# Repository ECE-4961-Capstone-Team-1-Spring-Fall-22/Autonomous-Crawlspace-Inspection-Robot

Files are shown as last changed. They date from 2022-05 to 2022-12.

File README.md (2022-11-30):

# Autonomous-Crawlspace-Inspection-Robot
This GitHub contains all relevant files used during development. For a comprehensive guide to the repository set up see the bottom of the document.
## Executive Summary
Crawl spaces grant convenient access to the plumbing, duct work, and electrical wiring of a house, but they often present unique dangers to maintenance professionals and residents alike. Exposure to harsh breathing conditions, hanging obstacles, uncomfortable working positions, and even animals can cause non-ideal conditions. This capstone project will focus on the design and assembly of a robot prototype that can perform these inspections autonomously. The end product will be an autonomous, mobile robot that can be left unattended in a crawlspace by an inspector. It will navigate through the space, create a map and model of the space, compile an image of the entire crawlspace ceiling, and collect sensor data. This sensor data will include humidity, temperature, and wood moisture content.

## Current Robot Capabilities
The first iteration of the project focused on setting up the hardware systems. Sensors, microcontrollers, motors, and power circuits were designed and implemented as part of a larger multi-group project. The following details the current capabilities of the robot.

* Low-level autonomy which allows the robot to navigate through an enclosed area
* Creating a map of the area using the SLAM algorithm
* Take pictures throughout an area and stitch simple areas into a singular, larger image
* Collect humidity, temperature, and moisture content data and overlay information on images
* Supply power for consistent operation across all components
* Robot movement through serial commands and return encoder data to the main microcontroller
* Manual control through text-based commands while also streaming live video to the operator

For more detail on current designs, see files in sub-system directories

## Salient Outcomes
Although this project includes lofty long-term goals, many exceptional systems were able to be incorporated in the first iteration of the project.
* The mapping was found to be accurate to 93% or more in each test that was run. While this is useful information for an inspector to have, it will also provide an invaluable framework for future updates to the autonomy
* Power was successfully applied to all parts of the system with no over-currents or under-voltages experienced by the system. All back EMF from the motors was successfully filtered out as well.
* Environmental sensing was found to be exceptionally accurate. Temperature and Humidity were both found to be 96% accurate or greater while moisture content was successfully measured to within 2.5% moisture.

## Pictures and Videos
The final system demo in the crawlspace can be found [here](https://www.youtube.com/watch?v=mYopD1X_bd8&t=9s)

A picture of the final system can also be found below 

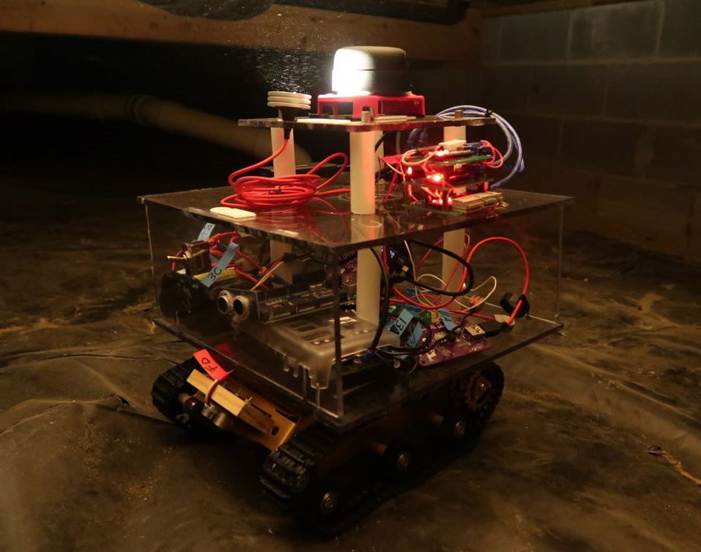
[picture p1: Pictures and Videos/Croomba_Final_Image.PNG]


## Who Are We? Mr. Jesse Robert's ECE 4961 Capstone Team 1

* James (Jim) Camp - Senior Electrical Engineering Major, Mechatronics Concentration - Environmental Sensor Subsystem Developer - Delegator 
* John-Caleb (JC) Williams - Senior Electrical Engineering Major, Electromagnetics Concentration - Navigation Subsystem Developer - Treasurer
* John Harris - Senior Electrical Engineering Major, Controls Concentration - Power Subsystem Developer - Secretary
* Joseph Thomas - Senior Electrical Engineering Major, Power Concentration - Movement Subsystem Developer - Social 

* Mr. Jesse Roberts - Professor and Faculty Advisor

* Project Stakeholders - This project was developed for anyone who needs to inspect their crawlspace. This includes homeowners, building inspectors, and renovators. The system is also a great solution for anyone experiencing issues with mold or unsafe crawlspace conditions.

# Repo Guide
This repository contains the entirety of the Autonomous Crawlspace Inspection Robot’s REV1 design files. The folder breakdown is as follows
* Design Files – Contains files that represent the final design state of the project. This is made up of an overall system schematic and the bill of materials (BOM).
* Documentation – Contains all written submissions created throughout both semesters of the course. Also included are the presentations used at the end of the project.
* Environmental Sensing – This subsystem is responsible for the data collection which occurs throughout the crawlspace. Additionally, image stitching is also included within this folder.
* Movement – This subsystem is responsible for controlling the physical motion and positioning of the robot. 
* Navigation – This system handles the mapping and autonomy. Interfacing with the Raspberry Pi, LIDAR, distance sensors, and remote access are also included in this subsystem.
* Pictures and Videos – A repository for all the pictures and videos taken throughout the experimentation and testing.
* Power - This subsystem is responsible for providing continuous power to all the components. Circuit protection and power filtering are also integrated into this subsystem.

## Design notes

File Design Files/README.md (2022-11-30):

# Design Files
This folder contains the system-wide designs as shown in a schematic diagram. It also includes the bill of materials (BOM).

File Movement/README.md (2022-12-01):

# Mechanical Movement System
The mechanical movement subsystem is essential for the operation 
of the Autonomous Crawlspace Inpsection Robot. The main purpose
of this system is to provide the robot with the ability to move.

# Specs, Design, and Analysis: 
This system has been designed to:

Communicate with the Navigation System where it receives directional instructions and sends back an instantaneous speed

Fit within the 16 inch height constraint and house all the hardware

Allow for variations in motor speed by using pulse width modulation

Move the robot forwards and backwards, and turn left and right

# Descriptions
An Arduino Mega is the microcontroller for this system. It communicates with the Navigation system, sends signals to the motor drivers, and measures the speed.

The design for the robot's chassis started with a robotics kit purchased from amazon, but it was customized and turned into the towered, modular design that is present today.

The Motor Drivers for the robot are the Cytron MD20A, which is an H-Bridge that can control the polarity of power applied to the motor as well as the average voltage through PWM.

The driving DC gearmotors are from pololu. They come equipped with quadrature hall effect motor encoders that can be used to measure the speed and direction of the robot.

This README file constitutes a summary, for detailed design information and analysis of each component see signoff files in this repository. A seperate README exists for the software in the relevant sub-directory.

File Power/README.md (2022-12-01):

# Autonomous-Crawlspace-Inspection-Robot
This branch documents the design process for the power subsytem. 

# Specs, Design, and Analysis: 
This system had the following requirements
* Provide +5V power to the logic electronics and microcontrollers
* Provide +12V power to the motor and mechanical system
* Prevent surges from creating system-wide failures
* Filter inconsistencies from the battery supply voltage and provide steady DC voltage to the components

The design of the system involved custom buck converters which allowed the use of both +12V and +5V power.
Fuses were used to ensure that power surges from one component would not negatively impact the other subsystems.
Terminal blocks were also used for their secure connections and ability to disconnect if changes were made. 

Analysis for the system can be found in the experimental data file.

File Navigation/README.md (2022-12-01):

# Navigation Subsystem 

## Specs, Design, and Analysis: 

This system is designed to use LiDAR and Ultrasonic distance sensors to navigate the inspection robot throughout a model crawl space while creating a detailed map of the surrounding environment. Additionally, the Navigation Subsystem handles USB communication with Arduino Mega/Nanos included in the Movement and Environmental Sensing Subsystems. The Navigation Subsystem MCU, sensors, wireless access point, and imaging hardware were chosen as hardware components capable of processing graphical heavy processing loads, complex distance measurements, and long-range communication protocols.  

The main MCU was required to run Ubuntu 20.04, the Robot Operating System (ROS), and visually heavy programs such as RVIZ and Gazebo. The 4 GB Raspberry Pi 4B was chosen for the Navigation Subsystem, as the CPU speed and RAM size were thought to be plenty for any computational needs. 

The distance sensors were needed to supply Python and ROS with exact and meaningful distance measurements that could be used to effectively guide the inspection robot throughout the crawl space. Moving at roughly 1 foot per second, the distance sensors were only required to supply 2 samples/second (via the Nyquist Theorem). The 360 Degree Slamtec RPLiDAR was chosen due to its high sampling frequency (KHz range), modularity, and readily available python based packages. The SeeedStudio Grove Ultrasonic Sensor was chosen due to the sensor output voltage of 3.3 Volts (maximum RPI GPIO Pin Voltage) and the included noise-filter for distance measurements.  

The wireless access point was needed to supply either a 2.4 or 5 GHZ wireless network, per FCC communication regulations. Additionally, the wireless access point (WAP) needed to supply a minimum communication range of at least 70 feet and a transmission speed of at least 100 mbps. The TP-Link N300 was chosen due to its maximum wireless transmission speed of 300 mpbs and its size, modularity, and power requirements (5 Volt 1 Amp).  

The camera was needed to provide detailed 720p or 1080p images and live video-feed for manual operation of the inspection robot. Additionally, the camera needed to be equipped with a medium/wide angle lens for capturing a large amount of information in the image of the crawl space ceiling. The camera also needed to be lit by a LED light so that the images would have enough illumination for post-processing and analysis. The SVPro 60 Degree HD USB Camera was selected for the imaging hardware due to its capability for high resolution images and fast autofocus. The Voltaic LED USB Emergency Light was chosen as the lighting hardware due to its modularity, size, light intensity, and power requirements (5 Volts 400 milliAmps).  

## Navigation Subsystem Components

Raspberry Pi 4B 4GB (Main MCU) 

Slamtec 360 Degree LiDAR (Distance Sensor) 

SeeedStudio Grove Ultrasonic Sensors (Distance Sensor) 

TP-Link N300 Travel Router (Wireless Access Point) 

SVPro HD USB 1080p Cameras (Ceiling/Wall Visual Capture Device) 

Voltaic USB LED Emergency Light (Camera Illumination) 

## Software, Signoffs, and Subsystem Schematic
The “Software” folder contains the Navigation Python script used to navigate throughout the crawl space, communicate with the Movement Subsystem Arduino, and take images of the crawl space ceiling. Also, this script allows the user to see live video-feed from the wall-oriented HD Camera if manual control is needed.  

The “Signoff” folder contains research, analysis, and validation of the chosen components  adherence to given constraints and specifications of the Navigation Subsystem.  

The “Schematic” folder contains a detailed KiCAD schematic of the Navigation Subsystem.

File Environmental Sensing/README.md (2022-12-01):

# Enviromental Sensing System

## Specs, Design, and Analysis:
This system is designed to collect 3 types of sensor data while also taking pictures of the crawlspace ceiling. The sensor data consists of the following
* Humidity
* Temperature 
* Wood moisture content

The humidity and temperature system consits of prebuilt sensors which interface with Arduino microcontrollers. However, the mositure content probe had to be custom built. It was made by creating a voltage divider that can switch the value of R1 depending on the range needed to measure. These three sensors each used their own microcontroller to maintain modularity.

A board stack was deisgned to allow for simple interfacing between the sensor modules. This works by using 3 PCBs which are sized the same and can be mounted on top of each other using 1 inch tall standoffs. The power connections for each board are passed throughout the staack using header pins with a long tail. This also allows for any new sensors to be snapped on top of the existing sensors and easily added to the system.

The final part of this subsystem is the image collection. Pictures are taken throughout operation and associated to a set of sensor data. The moisture content is displayed on each picture before being stitched together. Temperature and humidity are treated as an array and have the averages and standard deviations calculated. These values are then used to determine if any outliers exist and dispaly the location of these outliers on the images.

This README file constitutes a summary, for detailed design information and analysis of each component see signoff files in this repository.
A seperate README exists for the software in the relevant sub-directory.

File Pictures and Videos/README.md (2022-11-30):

## Pictures
This directory contains the pictures taken throughout the testing and experimentation phases of the project. 
This includes the images used for stitching, maps generated by the lidar, and general pictures showing our progress through the design

## Videos
A link to the OneDrive containing our experimental videos is found [here](https://tennesseetechuniversity-my.sharepoint.com/personal/jtroberts_tntech_edu/_layouts/15/onedrive.aspx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)

The final test run performed in a real crawlspace environment can be found [here](https://www.youtube.com/watch?v=mYopD1X_bd8). 
While this presented some challenges not seen in the model crawlspace, it was a test beyond the scope of our original project proposal. It achieved navigation and mapping results consistent with our expectations. The stops robot makes during the test are to allow for picture taking as well as data collection. This will be essential when the moisture probe arm is added to the system.

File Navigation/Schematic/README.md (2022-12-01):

## Navigation Schematic

Enclosed is the full KiCAD schematic of the navigation subsystem of the Autonomous Crawl Space Inspection Robot.

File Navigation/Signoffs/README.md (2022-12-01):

# Navigation Signoffs

Enclosed are the completed signoffs for the navigation subsystem of the Autonomous Crawl Space Inspection Robot. These signoffs were written to justify the chosen components adherence to constraints and specifications of the navigation subsystem. The chosen components for each signoff are listed below: 

## Main MCU
Raspberry Pi 4B 

## LiDAR
Slamtec 360 Degree A1/A2 RPLiDAR 

## Ultrasonic Sensors
Seeedstudio Grove Ultrasonic Ranger V2 

## Wireless Access Point
TP-LINK N300 Travel Router 

## HD Camera
SVPro 60 Degree HD USB Camera 

## Flashlight
Voltaic LED USB Emergency Light

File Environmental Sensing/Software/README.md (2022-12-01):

# Software Writeup

## What the code does
This file contains 4 programs that make up the environmental sensing system's software.
* The Temp Arduino file handles receiving data from the temperature sensor over I2C and sending that data to the main MCU using serial communication.
* The Humidity Arduino file handles receiving data from the temperature sensor over a single digital wire and sending that data to the main MCU using serial communication.
* The MC Arduino file handles the moisture content measurement. This code flips through 5 digital outputs to control the values of R1 in the voltage divider circuit. It takes resistance measurements at each point and averages the acceptable measurements before converting from Ohms to %MC.
* The Stitching python file handles the image stitching. The files are automatically sorted into an array and have their MC values overlaid on the image. The images are then stitched together by manually choosing which pictures were taken consecutively.
- This code also handles reading the temperature and humidity values from a text file, averaging the values, and displaying any values which are outside the acceptable range of 2 standard deviations.

## Dependencies
* Adafruit DHT Library (Arduino Internal)- Used to pull data from the humidity sensor over a single-wire data line. 
* Adafruit MCP9808 Library (Arduino Internal) - Used to pull data from the temperature sensor over I2C protocol. 
* https://github.com/KEDIARAHUL135/PanoramaStitchingP2 - Provided basic algorithm for stitching 2 images together and pulling images into an array.

# Code Instructions
For all Arduino codes, the instructions are the same.
1. Build a circuit using Arduino Nano based on the schematic found [here](https://github.com/ECE-4961-Capstone-Team-1-Spring-Fall-22/Autonomous-Crawlspace-Inspection-Robot/blob/main/Environmental%20Sensing/Environmental%20Sensing%20Schemat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)
2. Pull the Arduino file and place it in a folder with the same name as the code.
3. Download all relevant libraries by going into the "Sketch" menu, choosing "Include Library" and then importing the correct library from Arduinos internal system.
4. Set up the serial port by going into the "Tools" menus and choosing the correct device.
5. Upload code to the board.

The image stitching code instructions are as follows
1. Ensure that OpenCV and python are both downloaded and can successfully compile.
2. Places pictures in the folder called "TestPics" and ensure the folder is in the same directory as the program.
3. Ensure pictures are numbered 0 to max in order of taking.
4. Ensure the stitching lines in the code are set to match the pictures which you want to be stitched.
5. Run code, results will be shown in the plot initially but will be saved upon closing the plot.
* NOTE1: There are additional algorithms commented out that can be seen in this code. Each one was found the work for some cases and not for others.
* NOTE2: While this algorithm works for a straight view of an object, it was found in the late stages of development that perspective changes will cause issues. This is the topic of much research at the moment and further algorithm development will be necessary.

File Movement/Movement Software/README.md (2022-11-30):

# Mechanical Movement Software ReadMe
## What the Software Does
This Arduino Program accepts a serial input that is used to change the direction of the drive motors. 
This program uses Interrupts to measure the frequency of the Motor Encoder Signals.
Those Motor Encoder Signals are then converted to RPMs and Output to Serial.

## Dependencies
This program calls upon no additional libraries or other files.
Some form of serial input to the program is required for motor direction change.

## How to Install
This Program can be Uploaded to an Arduino Mega by using the Arduino IDE.
First, connect a USB cable between your computer and the Arduino Mega.
Second, in the IDE, under Tools, ensure that the board is set to "Arduino Mega or Mega 2560" the processor is the ATmega2560.
Third, ensure that the correct COM port has been selected.
Finally, in the IDE, click upload

## How to Run
The Program will immediately start outputting the speed, and it can be seen in the serial monitor.
The speed will consistently be 0 unless the interrupts are pinging.

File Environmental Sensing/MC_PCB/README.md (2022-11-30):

## Moisture Content Probe Module PCB
Enclosed are the Kicad files for the moisture content sensor PCB. This board is designed to be apart of and sensor board stack which uses the standoff parts found in the BOM. 
Terminal blocks are included to allow connection to the external circuit parts such as the motor driver and probe. Connections for these parts are found in the schematic pdf.

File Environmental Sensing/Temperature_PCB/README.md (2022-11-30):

## Temperature Module PCB
Enclosed are the Kicad files for the temperature sensor PCB. This board is designed to be apart of and sensor board stack which uses the standoff parts found in the BOM.

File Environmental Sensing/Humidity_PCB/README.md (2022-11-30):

## Humidity Module PCB
Enclosed are the Kicad files for the humidity sensor PCB. This board is designed to be apart of and sensor board stack which uses the standoff parts found in the BOM.

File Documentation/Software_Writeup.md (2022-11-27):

# Software Writeup
More detailed software descriptions can be found in the individual subsystem folders. Below is a high-level breakdown of the various software that is integrated into the system

## Navigation
* Autonomy
- Simple autonomy allows the robot to bounce around a space wihtout getting stuck
- Manual control is available through the command terminal in case of failure
* Mapping
- Robot Operating System (ROS) was used along with the SLAM algorithm to create a map
- This map can be visualized in RViz 
* Imaging
- The robot takes images of the ceiling at set intervals as it naviagtes
- These images are stitched together to create a wholistic view of the ceiling
- Live video is also streamed to a remote desktop in case of autonomy failure

## Enviromental Sensing
* Three programs were written for this system, one for each sensor
* The humidity and temperature programs required very simple code
- Programs recieved data from their respective sensors
- Data was sent to the main microcontroller through serial communication
* The moisture content probe took a resistance measurement
- This was done by switching through various R1 values in a voltage divider
- The final resistance value is converted to a moisture content and sent to the main microcontroller through serial communication

## Mechanical Movement
* An Arduino Mega handles the program which controls the motors
* Commands are sent from the main microcontroller to set the motor direction
* Encoder data is sent back to the Mega and Raspberry Pi so that the speed and position can be known

## Power
* No programming was necessary for the power system because it was purely hardware

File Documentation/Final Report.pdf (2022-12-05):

# Autonomous Crawl Space Inspection Robot Final Report

James Camp, John-Caleb Williams, John Harris, Joseph Thomas
Electrical and Computer Engineering Department Tennessee Technological University Cookeville, TN
jrcamp42@tntech.edu, jawilliams46@tntech.edu, jharris44@tntech.edu, jwthomas43@tntech.edu
I. INTRODUCTION
A. Problem Formulation and Motivation

The current inspection of crawl spaces requires the use of human time and effort, which could be seen as inefficient management of time as well as result in a lack of recorded measurements that could be useful in the analysis of the crawl space environment. Using the gathered background information, specifications, constraints, and a summary of already available solutions, an important problem with crawl space inspection can be identified as well as an appropriate objective to address the problem. An autonomous crawl space inspection robot could be created in order to better manage the time of individuals who would be inspecting the crawl space environment, as well as provide a record of important measurements taken from the environment. The objective of this capstone project is to create an autonomous crawl space inspection robot that is capable of navigating, traversing, and recording pictures, humidity levels, temperature levels, and moisture levels of a crawl space environment.

B. Background information

Much of the project’s importance lies within the scientific background associated with it. The scientific background also supplies the project with guidelines for the measurements and movement systems. The project will require background information in a variety of fields: biology, meteorology, and topography. Fifty percent of the air that cycles through the first floor of a home comes from the crawl space, so the air quality and status of the crawl space’s climate has a direct impact on the air that the residents of the home intake [1]. If the crawl space is a humid, cool environment then mold will be extremely likely to grow in those areas. Mold causes a multitude of negative health effects for humans including stuffy nose, cough, red and irritated eyes, itchy skin rashes, fever, and shortness of breath [2]. The robot will be able to make autonomous measurements that a technician can use to determine whether or not mold is likely to grow in those spaces, and the pictures taken by the robot will ideally be able to show any mold that is growing within the space. Every crawl space is different. Some spaces may have rocky, hilly terrain, whereas others may be flat but filled with puddles of standing water. With all of the different possible terrain that the robot may need to navigate, it is important that the robot be able to navigate in an ”all-terrain” fashion or be suited for the average crawl space, which consists of a dirt floor and is decently level. In some circumstances, animals and pests may take up residence within a crawl space. It is not within the scope of the project to have any sort of extermination methods, but that would be a possibility for future groups. In order for the inspection robot to navigate autonomously throughout the crawl space, it utilizes measurements of optical and sonic inputs from LIDAR and sound sensing. A light detection and ranging (LIDAR) sensor is a device that fires a narrow, infrared, pulse of light, commonly referred to as a laser, from a transmitter terminal. The LIDAR sensor then utilizes a clock in order to track the time taken for the pulse to refract from an obstacle back to a receiver [3]. A LIDAR sensor is commonly mistaken for a non-laser, infrared (IR) sensor, which utilizes infrared light in order to detect when an emitted beam is broken, revealing that an obstruction is present and outputting an appropriate logic signal [3]. Sound sensors, commonly referred to as ultrasonic sensors, utilize a clock, transmitter, and receiver in order to determine the distance from an object. Ultrasonic sensors are able to determine the distance from an object by tracking the time taken for a transmitted sound wave to be received after reflecting off an object [3]. These sensors can be used to avoid collision with walls and other obstacles in the crawlspace.
Mapping can be done using an algorithm called Simultaneous Localization and Mapping (SLAM)/ SLAM is an algorithm that allows an object to mark data points whenever an obstacle is reached. The device will continue placing data points until enough points have been marked for the device to develop a map and navigate throughout a room [4,5]. By utilizing physical and optical sensors, a device could develop an even more accurate map of the environment and increase the efficiency of its navigation.
Humidity, temperature, and moisture levels are relatively common measurements taken with module sensors designed for the Arduino microcontroller. The humidity of an environment is measured by applying an electric charge to a medium, placed between two electrode plates [6]. Depending on the level of resistivity, a humidity value can be determined, thus

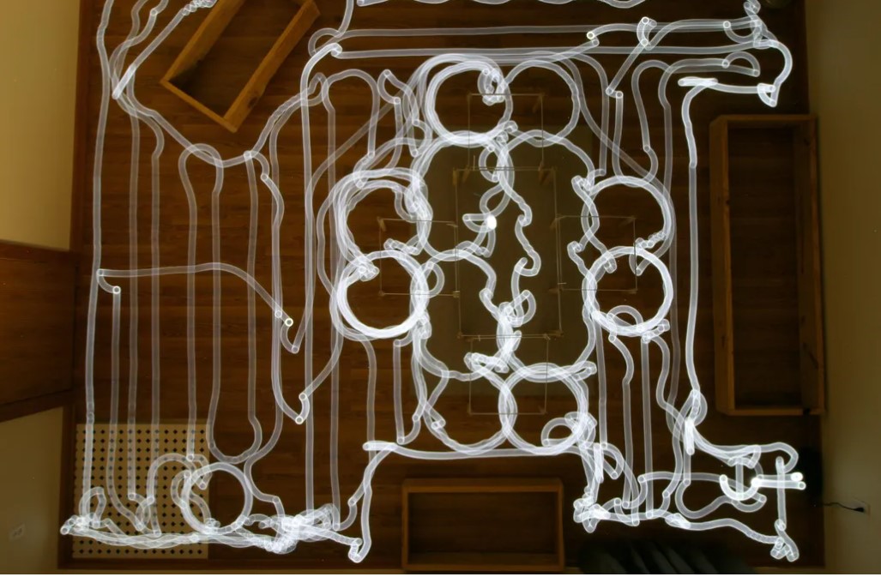
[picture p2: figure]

Fig. 1. SLAM Mapping [5]

allowing the humidity of an environment to be measured with a typical accuracy of five percent. Additionally, the temperature of an environment can be measured through the use of a thermistor, a resistor device whose resistance value has a direct, linear relationship to temperature [7]. Moisture levels are commonly measured in the same context as humidity levels. In order to measure moisture level, two probes are placed into a material or space and an electric pulse is sent between the probes of the device. The resulting resistance is measured and then a correlated moisture level can be determined [8].
The power system for this inspection robot utilizes a rechargeable battery as a voltage source. Buck converters can also be used to ensure the voltage source will be constant. These devices work by taking an input power and outputting a constant voltage with a current value that keeps the power equal on both sides of the device. Finally, fuses are devices that will fail at a certain current and turn into an open. This means that if an overvoltage is experienced in one branch of the system, that branch will be cut off and unable to affect the rest of the components.
C. Constraints

The crawl space inspection robot adheres to certain constraints and specifications in order to be deemed appropriate and properly designed. The average height of the crawlspace of a home ranges from 44 to 48 inches but can often be much smaller [9]. This limits how tall the robot can be to serve the maximum number of households. All components and wiring within the chassis must also be properly protected and sealed from water and dust exposure as these elements will be plentiful in most crawlspaces. The power system of the device was chosen to be able to supply the different voltage requirements of various components within the system, such as 12 Volt motors and 5 Volt controllers. It is also important that it can provide power long enough for the entire crawl space to be explored. Constraints were also placed on what frequencies can be used for manual control. This part of the system operates on 2.4 GHz to fit within the standardized frequencies which do not require a license [10].

Specifications were also placed on the robot by the team based on the planned robot operation. First, the device was designed to be shorter than 16 inches, or two blocks, to allow practical utilization of the device in almost any home. However, because crawl spaces can be 44-48 inches [9], the moisture probe will be able to extend at least 32 inches from the top of the chassis allowing it to fit in most spaces while also reaching most wooden beams. To ensure moisture content accuracy, feedback sensors will be added to the arm to ensure the probe is applied with the correct pressure at all heights. The batteries chosen allow for the system to operate for a minimum of four hours which should provide sufficient time to navigate the space. All parts, including the battery and sensors, were picked with heavy consideration of environmental ratings to prevent parts from wearing out due to dust, dirt, or moisture. For this reason, the battery will not have any exposed electrical contact points during operation in its final form. This specification will prevent rust and deterioration of the contacts from limiting the battery’s performance.

D. Overall idea

There are currently inspection robots available which can accomplish a variety of feats and assist individuals in the inspection of different environments such as crawl spaces. For example, one inspection robot currently available is the GPK32 Wireless Robot from SuperDroid Robots that is capable of capturing high resolution video for inspection through manual operation [11]. Additionally, another available inspection robot is the autonomous ExR-2 from Energy Robotics which is capable of autonomously navigating through a hard environment in order to provide video footage [12].
A major benefit over the existing robots is the addition of the sensor module. This module allows the robot to make the recordings an inspector would have to manually make otherwise. The module allows the ability to record more points and display the recorded data overlaid with a map of the crawlspace. This gives operators more information and presents it in a more useful and aesthetic way than plain numbers.
Another piece of technology utilized by the inspection and crawl space industry is a wood moisture probe which shows how much moisture is in the wooden boards underneath a house. In order to get moisture measurements from wooden boards, a person must manually push the probes into a board. The team’s robot will be able to perform this action autonomously which saves the operator from having any need to go underneath a crawlspace in the vast majority of cases. While there are currently solutions that exist and are available for purchase, the cost of these solutions is high, ranging from thousands to tens of thousands of dollars. There does not appear to be an affordable inspection robot that can meet all the required specifications given for this autonomous crawl space inspection robot.

E. Salient outcomes

Although this project includes lofty long-term goals, many exceptional systems were able to be incorporated in the first iteration of the project. The mapping was found to be accurate to 93% or more in each test that was run. While this is useful information for an inspector to have, it will also provide an invaluable framework for future updates to the autonomy. Power was successfully applied to all parts of the system with no over-currents or under-voltages experienced by the system. All back EMF from the motors was successfully filtered out as well. Environmental sensing was found to be exceptionally accurate. Temperature and Humidity were both found to be 96% accurate or greater while moisture content was successfully measured to within 2.5% MC. Finally, the movement system was able to control speed and direction with a linear speed of around 1.08 ft/s.

F. Report Organization

Firstly, this report consists of a literature review where the relevant information is detailed along with a critical analysis of that literature. Additionally, this report will discuss the team’s position in the industry setting, and the relevant engineering standards as well. Secondly, in consideration of the team’s methodology, the theory and overall idea of the solution, the complete design process, and other special items are discussed. Next, the project’s experimental results are displayed along with a small section of the deliverables. Then the logistics of the project are shown with a Gant chart, cost estimate, and final BOM. The report concludes with a discussion of the ethical and professional responsibilities, lessons learned, and a final summary of the project. At the end, each team member writes their own statement where he discusses the relevant information he acquired for this project either in other courses or otherwise.

II. LITERATURE REVIEW

A. Relevant Literature

Throughout the design of the Autonomous Crawl Space Inspection Robot, the capstone team consulted various pieces of literature for guidance on how to develop the best product possible. The literature examined by the capstone team ranged from online articles to papers to forums and various Github repositories outlined in this section.
A substantial portion of the project code was influenced by online robot operating system (ROS) and Arduino/Raspberry Pi forums. The robot operating system (ROS) wiki outlines, in detail, the process for developing a robot that can operate efficiently with Ubuntu and ROS [13]. From setting up Ubuntu 20.04 to what version of ROS should be used to library installation processes, the capstone team specifically followed all instructions and tutorials outlined in the main pages of the ROS wiki. Additionally, the team often consulted the

Ubuntu wiki for questions on installation, command line (shell) programming, and common instructions [14].
While determining how to develop a communication protocol for the inspection robot, team members often examined many pages of the Arduino/Raspberry Pi forums and wiki’s, which have a bountiful amount of helpful information for debugging USB and serial peripheral interface (SPI) library issues [15,16]. In fact, after spending countless hours debugging communication protocols for SPI, the team found forum and wiki posts that detailed common issues of implementing SPI and solutions for adapting the system to work with USB hubs within python [17].
In the beginning of the design and implementation of the inspection robot, team members simulated navigation and mapping algorithms with the commercially available Turtlebot 3 packages [18]. While these algorithms were not explicitly implemented into the inspection robot’s design due to compatibility issues, the information supplied by Turtlebot served as a helpful introduction to ROS, SLAM, and Autonomous SLAM. The Turtlebot 3 E-Manual was specifically helpful to the capstone team, as this document outlined the processes of getting started with Ubuntu, ROS, and various forms of SLAM [19]. Additionally, the Hackaday article, “Build Your Own Turtlebot 3 Backbone”, served as a great guide for implementing custom ROS and Arduino packages to communicate with a robot over ROS manual control protocols, such as turtlebot teleop keyboard control [20].
One of the largest helps with implementing Hector SLAM into the Autonomous Crawl Space Inspection Robot was the following ROS wiki/forum posts, which outlined in detail the specific parameters that needed to be changed within the header files of ROS and Ubuntu libraries [21,22]. Without guidance from these online sources, team members would have struggled much more with implementing a mapping system onto the robot in ROS. While these sources may not be typical academic papers, the individuals writing the forum/wiki posts have a large amount of knowledge which the capstone team found to be extremely helpful in the success of their Autonomous Crawl Space Inspection Robot.
B. Engineering standards

It is vitally important for the team to understand the standards put in place by the government and engineering societies because they act as restrictions and guidelines for the design of the robot. The IEEE sections 1872.2-2021 and 7007-2021 on autonomous robots and ethically driven robots and automation as well as the NEC within the NFPA in particular will have the greatest effect on the robot. The team will need to be familiar with the content of the above standards in order to create a product that adheres to the code of conduct specified in those standards. For example, Article 310.10.C of the NEC states that insulated conductors and cables used in wet locations shall be moisture impervious or metal-sheathed or be of a type listed for use in wet conditions. Furthermore, section 310.14 contains the requirements for Ampacities for conductors rated 0-2000 Volts [23]. The constraints described in these sections and others will have a direct impact on the design of the Autonomous Crawl Space Inspection Robot.
Along with the design, the assembly of the first prototype will also have to follow industry standards. IPC sets international standards regarding the assembly of everything from soldering to Printed circuit boards (PCBs) [24]. Because this product will need to have a long lifecycle but does not perform any health or safety-critical operations, it will be classified as an IPC class 2 product. One member of the group holds an active certification in IPC-J-STD-001 and will be responsible for inspecting all soldering and PCB assembly to ensure compliance with the standard.

III. METHODOLOGY

A. Theory and Overall Idea of your Solution

To develop a working autonomous inspection robot, team members began the design process by researching commercially available products that possessed similar capabilities with what was to be designed by the team. Household autonomous vacuums, such as the iRobot Roomba, were thoroughly examined along with the navigation and mapping algorithms implemented onto the devices. Additionally, team members compared commercially available inspection robots, such Husky and SuperDroid, to determine the “common practices” for developing an industry-ready inspection robot. The power and mechanical systems of these devices were also investigated by team members so that appropriate specifications and constraints could be created for the design process. Finally, handheld moisture probes were examined so that customized hardware could be created for the robot to use for measuring the moisture content of the crawl space ceiling.
After completing their literature review, team members agreed on what parameters would be best fit for the inspection robot and a design plan was put into place for each subsystem. The Navigation subsystem was to utilize a Raspberry Pi 4B, equipped with Ubuntu 20.04, robot operating system (ROS), Python 3.7, light/sound sensors, and Hector Simultaneous Localization and Mapping (SLAM). The Mechanic subsystem was to utilize a tank like chassis, an Arduino micro-controller, and two motors/motor drivers. The Environmental Sensing subsystem was to utilize commercially available temperature and humidity sensors, along with a custom designed moisture content sensor. The Power subsystem was to use a 12 Volt 6.6 Amp-Hour battery, along with custom designed buck converters and fuse boxes.
By combining the previously mentioned subsystems, the Autonomous Crawl Space Inspection Robot would be a device capable of navigating autonomously throughout a model/actual crawl space environment at a speed of roughly one foot per second, while simultaneously generating a two-dimensional map. Additionally, the inspection robot would be capable of collecting images and temperature, humidity, and moisture content readings of the crawl space and its ceiling structure. Finally, the robot would be able to operate for over two hours of full run time and be controlled wirelessly if manual control is needed for mapping success or robot recovery.
B. Complete Design Process

Before jumping in to a detailed design, the team looked at the high level view of the project. Using this method, a plan was put in place for what systems would be included in this iteration of the project. It was also decided which interconnections would be needed between each part in the system to ensure that all parts chosen in the detailed design could interface with each other. Once this high-level design was completed, the team was able to move into it’s detailed design phase.
The detailed design process focused on modularity which allowed the design to be parallelized. This means that each group member was given a subsystem that could be designed largely separate from the other subsystems allowing for maximum efficiency in the design. Modularity also ensures that errors in the separate subsystems will have as minimal an effect as possible on the other parts of the project. Following this principle, four subsystems were chosen for the design: power, navigation, sensing, and movement.

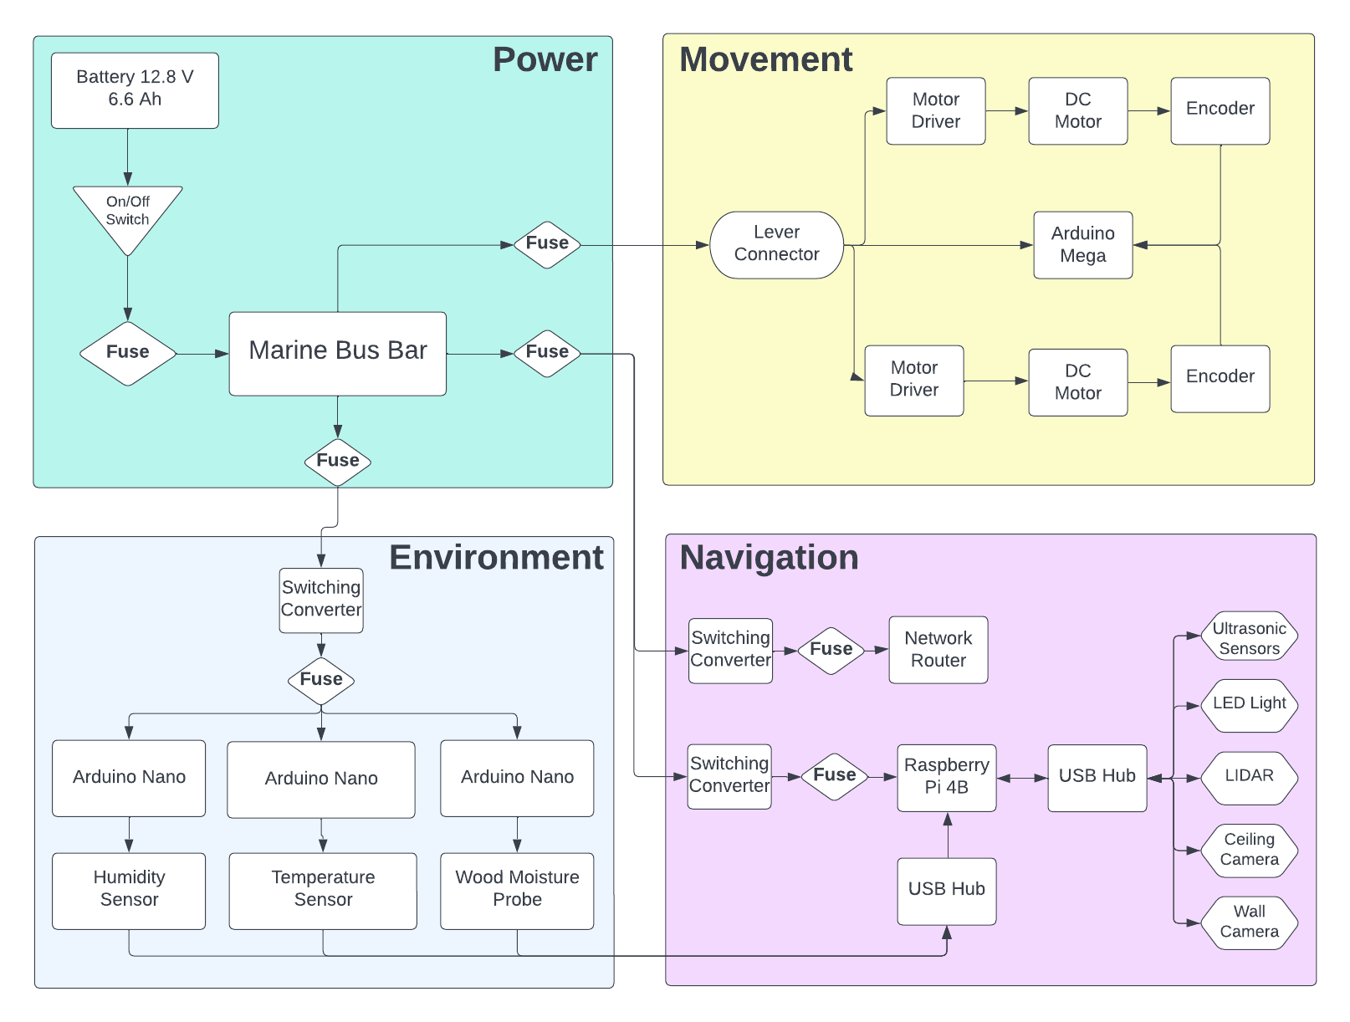
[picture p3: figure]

Fig. 2. Model Crawlspace

The hardware of each subsystem was designed concurrently during the design phase 2 period. After the individual designs were approved, the group shifted focus to interfacing the modules and ensuring that all information and power that needed to pass between systems was able to. This process brought the electrical design of the system to a close. From that point, the physical system had to be mechanically mounted. A multi-tiered system was chosen as it allowed us plenty of space for all parts. This mounting system also allowed each sensor to be placed at varying heights based on its individual

requirements.
The final part of the design was the software. While a basic framework had already been created for much of the system’s code, this portion was unable to be fully operational until the hardware was ready to be tested. For this reason, the bulk of the software writing had to wait until the majority of the hardware assembly was complete. The software used Robot Operating System (ROS) which is a mid-ware designed to run a variety of robotic systems. This program handled mapping while separate code was written in python to allow for autonomy, image collection, and image stitching. Finally, the code to collect environmental sensor data and control the motors was written in C on the Arduino IDE. Because the system included five separate microcontrollers, most of these pieces of code are running independently of each other. This meant that the last step of software design was interfacing with the different programs. Once this was complete, a final test run could be completed in a realistic crawlspace environment.
C. Design Considerations

During the design process detailed above, many factors had to be taken into consideration. The most obvious of these considerations was the professional standards explained earlier in the report. Outside of standards, safety was also taken into consideration as the robot will be operating in peoples home. The power system had to take precautions such as circuit protection and appropriately gauged wires to prevent fires from occurring on board. The autonomy program also had to be written to avoid collisions in order to prevent damage to the home.
Another design consideration was the environmental and economic impact of the project. Because the robot is solely operating underneath homes, the only environmental impact the team needed to consider was the parts purchased. When possible, all parts were chosen to be ROHS compliant to ensure minimal environmental impact from the robot. As for economic impacts, some concern was given to the possibility of the robot taking jobs from the inspection industry. However, an operator would still be needed to drop off the robot and inspect the results. This means the Croomba would only require the retraining of inspectors and not a full replacement.

IV. RESULTS AND DISCUSSION

A. Experimental Results

POWER

In order to verify the power subsystem is meeting all requirements, 5 trial runs measuring the voltage and current of each main subline coming off the battery were carried out, and the results are in the tables below. Over an hour and fifteen minutes of trial runs were performed while programming. The power system successfully powered all subsystems without outside assistance for the duration of these tests. This proves the two constraints laid out in the proposal that the power subsystem will provide correct current and voltage to the subsystems for a time that would allow mapping of a crawlspace environment.
Main Power LN 2 & 5
Trial Number (N) | Current(A) | Voltage (V)
1 | 0.526 A | 13.26 V
2 | 0.627 A | 13.26 V
3 | 0.675 A | 12.85 V
4 | 1.265 A | 12.68 V
5 | 1.326 A | 12.75 V

Navigation LN 7A & 8A

Trial Number (N) | Current(A) | Voltage (V)
1 | 0.7 A | 5.33 V
2 | 0.6 A | 5.34 V
3 | 0.79 A | 5.33 V
4 | 0.7 A | 12.68 V
5 | 1.326 A | 12.75 V

Network Router LN 9A & 10A

Trial Number (N) | Current(A) | Voltage (V)
1 | 0.1 A | 5.3 V
2 | 0.12 A | 5.32 V
3 | 0.12 A | 5.31 V
4 | 0.28 A | 5.31 V
5 | 0.33 A | 5.3 V

Movement LN 11A & 12A

Trial Number (N) | Current(A) | Voltage (V)
1 | 0.526 A | 13.26 V
2 | 0.627 A | 13.26 V
3 | 0.675 A | 12.85 V
4 | 1.265 A | 12.68 V
5 | 1.326 A | 12.75 V

Environmental Sensing LN 13A & 14A

NAVIGATION

The Model Crawlspace

To test the navigation functionality of the autonomous crawlspace inspection robot, a rectangular-shaped model crawlspace was created, with a length of 16.5 ft, a width of 6 ft, and a resulting area of 99 square feet. Floor tiles were used as a reference for quantifying the crawlspace area, with each floor tile having an area of 9 in by 9 in. The walls of the model crawlspace were made with various materials available

Trial Number (N) | Current(A) | Voltage (V)
1 | 0.0642 A | 5.24 V
2 | 0.0645 A | 5.23 V
3 | 0.0644 AA | 5.26 V
4 | 0.0.065 A | 5.31 V
5 | 0.064 A | 5.3 V

in the laboratory and had a minimum height of 17 in and a maximum height of 36 in.

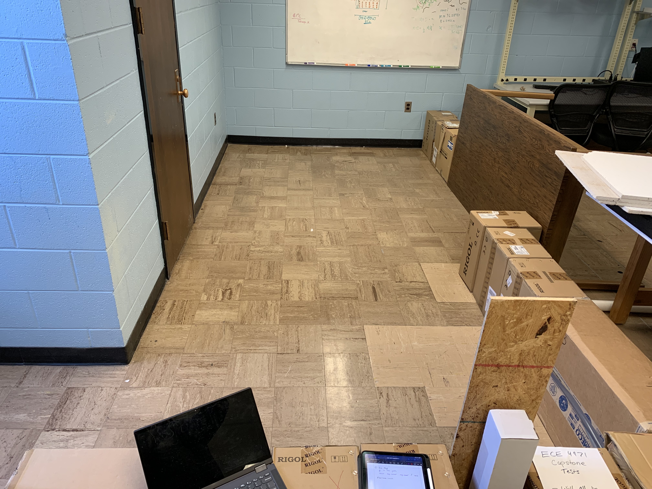
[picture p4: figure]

Fig. 3. Model Crawlspace

Mapping

The main job of the system’s lidar is to create a map of the surrounding area without having to be provided a manually drawn map by the operator. To ensure that the map is being generated correctly, the perimeter of the test area was found by measuring the picture at a set zoom and creating a proportion from that value, and the percent error was calculated. The areas missed were then measured on the screen and the proportional value was applied to convert into the physical distance. The focus of this experiment was to identify the areas along the perimeter that the lidar missed as the additional points it caught past the perimeter are blocked by the true wall.

Perimeter (ft) | Measured Perimeter (ft) | Percent Error (%)
47.75 | 45.74 | 4.39
41 | 38.63 | 6.14
41 | 38.68 | 6.00

The results show that the lidar was able to successfully map the majority of the perimeter as it navigated throughout the crawlspace. In the worst case, the robot only failed to map 6.14% of the model environment. However, this percentage should be mostly negligible because none of the gaps in the walls of the model crawlspace are large enough for the robot to fit through.

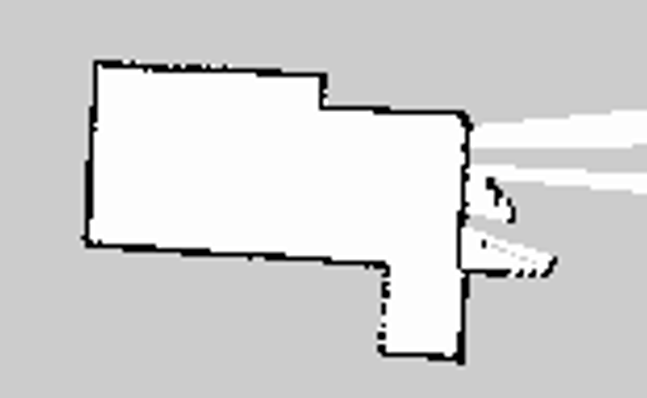
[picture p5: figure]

Fig. 4. Model Crawlspace Map

Maneuvering

In adherence to movement specifications, the robot needs to be capable of maneuvering through 70 % of the model crawlspace. To test adherence to this requirement, the team members counted which of the floor tiles in the model crawlspace the robot had not touched, and therefore how much of the total area of the crawlspace the robot had not maneuvered through. Additionally, the robot was initially placed in different corners of the model crawlspace to test the behavior from different initial positions.
In this experiment, the total area of the crawlspace was roughly 100 square feet and the total area covered by the robot is calculated and listed, along with the total percentage of the crawlspace area covered during the test. It is worth noting that in addition to the area listed in the table below, the robot often crossed back through past squares, effectively increasing the total area covered by the robot.
Area Where Present (ftˆ2) | Percent of Area Covered (%)
86.50 | 86.50
91.00 | 91.00
82.00 | 82.00
76.38 | 76.38
85.94 | 85.94

As shown in the above table, the crawlspace inspection robot was able to maneuver through more than 70 % of the model crawlspace area, often maneuvering through more than 80 % of the space without getting stuck or needing assistance from the operator. It is important to note that while the robot did not enter 100 % of the tiles in the crawlspace area, not every tile must be entered for an incredibly detailed map to be created within the ROS software using the LiDAR sensor.

Imaging Quantity

After adjusting the project’s scope, imaging has been reprioritized and will take precedence over autonomous control. Because the plan is to stitch the images of the crawlspace together using python and OpenCV, it is essential to find what percentage of the ceiling can be successfully photographed. This metric was tested by treating the photographs taken as a jigsaw and then finding the area of any spots not recorded and comparing that area to the overall ceiling area.

Total Ceiling Area (ftˆ2) | Pictures Taken | Area Pictured (ftˆ2)
87 | 33 | 7920
87 | 36 | 8640
87 | 54 | 12960
87 | 51 | 12240
87 | 42 | 10080

After allowing the robot to run its course, the number of pictures taken can be seen in the table above. The real area captured by each picture was then multiplied by the number of pictures taken to find a value for the full area pictured. While this value will feature some overlap, it is significantly large enough to convince the team that the robot saves pictures that will cover the entire ceiling area. Along with this metric, the photos were flipped through and ceiling landmarks were used to confirm that no part of the ceiling was missed.

Imaging Quality

Python code was created using the OpenCV library to perform the image stitching. This test was performed using both real pictures taken of the ceiling using the robot’s camera and pictures of a crawlspace ceiling. This allows us to confirm that the code will work both in a real crawlspace setting and will also work when using the camera.

Compared Pictures | Percent Overlap (%)
Test 1, 1 and 2 | 56
Test 2, 1 and 2 | 55
Test 2, 3 and 4 | 45
Test 2, 5 and 6 | 52

Tests were performed on the pictures taken to find the necessary overlap percentage between pictures. It was found that this overlap was around 50% for all the stitchings that worked correctly.

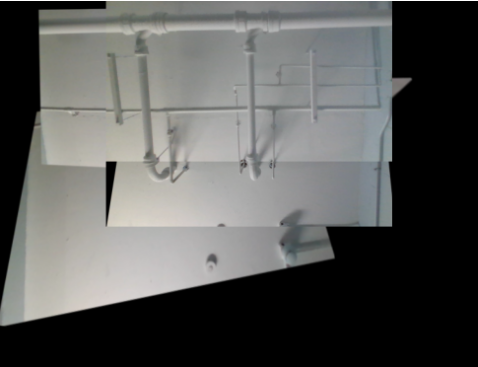
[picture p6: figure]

Fig. 5. Model Crawlspace

Wireless Access Point

The main job of the system’s wireless access point is to create a wireless network for communication between the system’s main control, the Raspberry Pi, and the system operator in the case that manual control is needed. Adhering to the given constraints, the wireless access point operates on 2.4 GHz and is a private network that requires a password for use. To ensure that the wireless access point was sufficient for use, the distance and overall connectivity, and control were tested four times.
In each of the four tests, a laptop was connected to the Raspberry Pi at a distance of 100 feet, first on the fourth floor of Brown Hall and then on the third floor of Brown Hall. The robot was pinged by the laptop with 32 bytes of information, and the response time in milliseconds from the computer to the Raspberry Pi and back was recorded. Finally, the overall system control was tested by opening applications and interacting with the system peripherals such as one of the USB cameras over Microsoft Windows Remote Desktop Protocol.
Distance From Robot (ft) | Average Ping Time (ms)
100 | 4
100 | 3
100 | 3
100 | 3

The results show that the wireless access point is sufficient for the application of the crawlspace inspection robot and that operators will be able to successfully control the robot from well over 70 feet away, allowing for manual control in more significant than average home crawlspaces, which would only require a max communication distance of 70 feet.

ENVIRONMENTAL SENSING

Temperature

The sensor was placed outside at different times and compared to the ambient temperature given by Weather.com. The test was performed like this because the commercially available sensor turned out to be incredibly slow and inaccurate. It was also done in this way because an outdoor environment is where the robot will be used.

Sensor Temperature (°F) | Listed Temperature (°F) | Percent Error (%)
62.825 | 63 | 0.28
61.5375 | 61 | 0.88
57.925 | 59 | 1.82
62.2375 | 64 | 2.75
71.125 | 70 | 1.61
66.6875 | 67 | 0.47
66.5375 | 64 | 3.96
65.53 | 66 | 0.71

The table shows that the system temperature sensor has exceptional accuracy when compared to a purchased sensor.

The max error found was just under 4% which is well within the desired level of accuracy.

Humidity

The sensor was placed outside at different times and compared to the humidity given by Weather.com. The test was performed like this because the commercially available sensor turned out to be incredibly slow and inaccurate. It was also done in this way because an outdoor environment is where the robot will be used.

Humidity Sensor (%RH) | Listed Humidtiy (%RH) | Percent Error (%)
82.3 | 84 | 2.02
87.1 | 89 | 2.13
93.1 | 95 | 2.00
86.9 | 86 | 1.05
83.2 | 84 | 0.95
95.4 | 99 | 3.64
92.8 | 96 | 3.33
37.5 | 38 | 1.32

The table shows that the humidity sensor is well within the desired range for accuracy. The datasheet for the DHT22 sensor says the accuracy should be ±2 %RH. While this experiment found several points outside this range, it seems to mainly be at the higher humidity values where the accuracy decreases. However, even at these points, the accuracy is at a very acceptable level.

Moisture Content

The Moisture Probe was first tested using axial resistors so that a known value could be tested. The resistors were also checked on a multimeter so that the true value could be compared along with the listed value. This test provided limited results due to the availability of resistors to test. However, it is secondary to the full moisture content testing and was mostly used for troubleshooting.

Multimeter Result (MΩ) | Probe Result (MΩ)
1.02 | 1.02
2.23 | 2.23
4.83 | 4.82
9.88 | 9.78
51.0 | 46.0

The results above were all found to be accurate within 1% error except for the 47 MΩ test which had about 10% error. This is because it was found that the first two stages had greatly increased accuracy compared to the stages with larger resistors used in the voltage divider. After much research, it was found that Arduino analog read pins prefer a smaller input impedance which was unknown at the time of design. This could be fixed in future revisions by switching out the microcontroller used.
The system was used on blocks of wood with differing moisture contents and compared to the results given by a commercial wood moisture probe. Forcing a piece of wood to be a certain moisture content caused some problems with this experimentation. Leaving the wood pieces in a steamy room allowed values between 7% and 11% to be tested but the higher values could not be achieved this way. Instead, a piece of wood was soaked with water and tested at different times as the wood dried out and its moisture content fell. This allowed the higher values to be tested.
COTS Moisture Content Probe | System Moisture Content Probe
7 | 6.86
9 | 7.34
10 | 8.13
10 | 8.31
11 | 9.51
13 | 11.31
13 | 14.44
14 | 15.89
15 | 12.26
16 | 17.55
17 | 16.87
19 | 18.55
24 | 22.4
25 | 23.26
26 | 23.54

As can be seen from the table above, the actual moisture content value is not 100% accurate for the commercial probe. However, all values fall within ±3 of the expected percentage value. The collected data shows that the system is detecting changes within the moisture content of the plank. Based on the raw resistance values which were seen in the previous section. It is believed some of this error comes from the equation created to convert resistance to wood moisture percentage.

MOVEMENT

The Height Constraint

For the first test, the height of the robot was measured with a tape measure. This was done to ensure that the 16-inch height constraint was met. This experiment was conducted twice and the results are displayed below.

Trial Number | Height of Robot
1 | 15.1875 inches
2 | 15.1875 inches

The above results show that the robot is 15.1875 inches tall. That number is less than 16 inches, and thus the height constraint has been met.

Motor Encoders

The purpose of this test is to confirm that the motor encoders and Arduino software are correctly measuring the rotational speed of the motors. The motor encoders are connected to GPIO pins on the Arduino, and the software reads the frequency of the signals and converts them into a rotational speed that is displayed on the serial monitor. Those values were compared against a measurement obtained by using a digital tachometer placed in contact with the drive wheel. The values in the table below are in units of RPMs.

Robot’s Reading | Tachometer Reading | Percent Error
219.7 | 220 | 0.136%
218.5 | 219.2 | 0.319%
220.1 | 219.8 | 0.136%
219.2 | 219.9 | 0.319%
220 | 220.6 | 0.272%

These results show that the Arduino program for the motor encoders is correctly measuring its speed.

Linear Speed

For this experiment, the team wanted to measure the robot’s linear speed. The desired speed is about 1 foot per second. To do this,10 feet was measured with a tape measure and then used a stopwatch to determine how quickly the robot covered that distance. This gives us the average velocity of the robot. The measured values for average velocity were also compared to the instantaneous RPMs that were displayed in the Arduino Serial Monitor while the robot was in motion. Those values were recorded and are displayed below. The RPMs are also converted to feet/second for ease of comparison.

Travel Time | Average Speed(ft/s) | Instant. Speed(ft/s) | Percent Error
9.75 | 1.03 | 1.09 | 5.505%
9.68 | 1.04 | 1.07 | 3.21%
9.71 | 1.03 | 1.088 | 5.331%

These results show that the average speed of the Croomba is about 1 foot per second which is the desired value.

30 Degree Incline

Finally, a test was done to determine whether or not the Croomba could ascend a 30-degree inclined plane as described in the signoffs. To accomplish this, the team put together some pieces of plywood at a 30-degree angle and set the Croomba on a course to see if it could make its way up the hill. This test was conducted 3 times.
The Croomba was unable to go up the steep slope. The team believes this deviation is caused by a lack of traction on the treads as well as a high center of mass on the robot. That high center of mass pulls the robot back down the hill and the front of the bot begins to lose traction with the ramp. In short, the robot is too top and back heavy, and this leads to the robot wanting to flip onto its back like a turtle when ascending the incline.
However, the team conducted additional experiments by lowering the angle of the incline to find the maximum angle that the robot could traverse. All of the results are displayed in the table below.
Incline Angle | Croomba Ascension?
30 | No
30 | No
30 | No
25 | No
20 | No
15 | Yes!
15 | Yes!
V. PROJECT DELIVERABLES

In the project proposal, the team stated that they will produce a robot that will autonomously navigate through a simplistic crawl space with only a few obstacles present, collecting sensor data at certain intervals, and taking pictures that cover the majority of the crawl space. The objective of this capstone project is to design a robot that will utilize optical and physical sensors that measure distance in order to navigate throughout a crawlspace environment, while simultaneously recording different environmental measurements including: humidity, temperature, and wood moisture levels.
Now at the end of the project, the team has delivered the robot described above along with additional features such as image stitching and remote control. The team has also prepared the way for future renditions of this legacy project by making their designs with a focus on modularity.

VI. TIMELINE AND COST ESTIMATES OF THE PROJECT

When planning the design, the drving factor was the importance of each system. The very first signoff submitted focused on choosing the main controller for the entire robot as every other system would depend on that design. From there, each group member wokred on their individual design while keeping in mind what information would be needed by later steps. For example, much of the power system had to be designed later in the process because it depended on how much current the other systme components would require. Following this process allowed us to have minimal issues with pieces of the system not meshing in the assembly stage. The Gantt chart found in Appendix 1 details the stages of design which were loosely followed during that stage of design.
As the design matured, team checks had to be performed on each subsystem. Signoffs were shared between the team in order to ensure everything was double checked before being submitted. The group also held weekly meetings in which all members were updated on the changes happening in individual subsystems. These meetings also allowed the team to discuss system-wide decisions and ensure everyone was on the same page.
Budget had to be considered along with the timeline to ensure that the team spent a reasonable amount of money during the design. During the project proposal, a estimated budget was created to give a minimum and maximum estimation for the project. These estimates came out to $425 and $1097 respectively. After completing the project, a new budget was made which can be found in Appendix 2. It can be seen that the team spent about $763 which was within the budget estimated at the start of the project. However, this number does not include several parts included on the robot which did not have to be ordered including the Raspberry Pi and the battery. Once these parts are included, the actual cost is estimated to be around $1155. This would have put us slightly over budget if all parts had needed purchase

VII. ETHICAL AND PROFESSIONAL RESPONSIBILITIES

Damage to a person’s home is the primary ethical consideration for this project; thus this consideration has affected many design decisions. The power system has redundant fuses to protect the wires from overcurrent and prevent any possible fire hazards that could result. The size, speed, and weight of the robot have been considered. A large, rampaging robot is a much more serious risk than a small controlled one. Limiting the robot’s size and regulating the speed at which it operates ensures that important structures under the home are not damaged because the robot is incapable of generating the force required to do so.
Another major concern with sending a robot through a client’s house will be privacy. Network privacy will be protected by using a separate, local router when further communication needs to be implemented for the manual control video stream. This video stream will also only be activated during times of manual control and will not include audio to avoid the recording of private data. Although this addition will likely not be a part of the first prototype, these considerations will be kept in mind throughout the hardware design to set the basis for future development.
The final ethical consideration is given to industry impact. Since the goal of the product is to automate a task normally carried out by a person thought had to be given on how this might impact the job market. This version of the robot was designed to be semi-autonomous. Meaning it still requires human interaction to operate. With this in mind, it is believed that the CROOMBA will have a positive effect on the job market by allowing home inspection business to operate more efficiently.

VIII. LESSONS LEARNED

Throughout the ECE 4961/4971 Capstone Courses, the Autonomous Crawlspace Inspection Robot Team has experienced many difficulties, which allowed for positive reinforcement of best practices and some interesting learning opportunities. The most significant lesson learned occurred one evening, during a test of the power draw on the robot, the LiDAR sensor contacted the ammeter probes and was shorted through the USB ports of the Raspberry Pi 4B and back to the battery. The short caused damage to the RPi and the LiDAR sensor, both of which had to be replaced. Additionally, the microSD card connected to the RPi was corrupted. After many hours, the team was able to recover/recreate the ubuntu system and navigation algorithms. While this was disheartening at the time, the team members learned to be more careful with measuring current and voltage on a moving system as well as the importance of regularly backing up code.
The mechanical movement subsystem experienced a setback with utilizing real-time interrupts (RTI) on the Arduino microcontroller. By interfacing with speed sensing, RTI, and direction controls on one microcontroller, the RTI often caused the program to stop and become stuck within the interrupt functions. To solve this problem, team members discovered a way to detach and reattach the interrupts within the Arduino software, slowing down the program in the process. While the current use of RTI within the motor code works, the team members believe this program could be made much more efficient by using more than one microcontroller for controlling interrupts, speed, and changes in direction.
For the environmental sensing subsystem, building the wood moisture probe required significant research into different methods for measuring resistance. Thanks to this research, the sensor worked well with the first iteration while providing a lesson in designing a circuit. On the other hand, one of the most significant issues with this subsystem came from the PCB design. The first iteration of the boards had many problems including incorrect footprints, plugs that were hard to access, and misaligned parts. These problems provided invaluable lessons in PCB design but unfortunately came after the parts had already been ordered.
The navigation subsystem experienced issues with implementing common autonomy packages and previously simulated navigation programs into ROS. While the Hector p algorithm is currently working with ROS to generate detailed maps, the team members were not able to get 2D navigation goals to work with the current iteration of the robot, instead relying on a custom python navigation program. If time permitted, the team feels confident that a custom ROS package, based on the official ROS wiki tutorials, could be created for the robot which would allow for Autonomous SLAM to be implemented.

IX. CONCLUSIONS

Crawl Spaces are an important but often forgotten section of a residential home. The environment and climate of a crawl space not only have a direct impact on those that live in the home, but also on the professionals that are exposed to the crawl space environment. The purpose of this capstone project is to provide a safer, more efficient, and autonomous method for collecting environmental data within a crawl space. The Autonomous Crawl Space Inspection Robot is an effective solution to the problem formulated throughout this document. The robot was able to successfully map out a variety of different environments while navigating autonomously through the space. Base-level image stitching algorithms were implemented to create a holistic image of the area’s ceiling. While moving throughout the crawlspace, the robot collected sensor data to be visually represented on the stitched picture. Backup systems have also been implemented to allow the robot to be manually controlled in case of autonomy failure. Finally, the power system successfully filtered the supply to provide the constant voltages necessary for operation.
The modular nature of this project provides many opportunities for future work to be implemented on later iterations of the robot. Possible new features include upgrades to the hardware, a higher level of autonomy, improved chassis, and additional hardware for the sensing system. The image stitching algorithm will also be improved in future iterations. The Autonomous Crawl Space Inspection Robot will become a legacy project that future teams will continue to develop.
A. Individual Statements

I was responsible for the movement subsystem, which included the design and analysis of the motors, motor drivers, microcontroller, and chassis. My other courses prepared me for capstone in a variety of ways. My understanding of electric circuits from circuits 1 and 2 as well as electronics was particularly helpful. My experience with arduino programming from CSC 1300 and ECE 4370 was useful in the development of the movement system. I used the knowledge of motors and other electrical machines that I gained in ECE 3610 when selecting the drive motors in the system. Over the course of the project I gained new knowledge in numerous areas foremost in the aspects of mechanical power and serial communication. I learned most of the new information by researching the internet, but I learned from my teammates as well. - Joseph Thomas
I was responsible for the navigation subsystem, which included the implementation of the navigation hardware (Li-DAR, HD Cameras, Ultrasonic Sensors, Raspberry Pi 4B, WiFi Router, and Flash Light). I was also responsible for the design of the navigation and mapping algorithms within ROS and co-authored the navigation algorithm in Python. Throughout this course, I was able to apply knowledge gained from past courses such as Optoelectronics Engineering and Electromagnetic Fields 1 and 2 when dealing with the LiDAR and Ultrasonic Distance protocols of the navigation subsystem. Additionally, when creating the private communication network, I was able to apply knowledge and skills from the Intro to Telecommunications. Additionally, when working with Joseph on the Movement subsystem, Finally, throughout this project, I have gained extensive knowledge with the Linux operating system Ubunutu, the Robot operating System (ROS) midware, and an overall sense of programming/troubleshooting complex robotics systems - JC Williams
I was responsible for the design of the power subsystem. I was also responsible for arranging the wires in the case in an efficient and effective manner using line numbers to aid in this task. I used alot of the material learned during the course of my undergraduate degree. Additionally, I was grateful for Mr. Robert’s suggestion to make the buck converters for the project. Finally, throughout this project, I have gained extensive knowledge of what it can be like to collaborate with an engineering team to accomplish a goal. I have been lucky to work with such a mature group of people for the past two semesters and will always look back at the experience with a ”certain” fondness. - John Harris
My subsystem was the environmental sensing system This system handled receiving and processing temperature, humidity, and moisture content data. I also took over the image stitching and developed algorithms to form the basis of future work in this area. Because my system contained a mix of electrical, mechanical, and software, I had to pull information from a variety of sources. The main classes which informed my design were electronics, microcomputer systems, dynamics of machinery, and embedded systems. I also gained new knowledge in how to measure moisture content, cascading rail systems, OpenCV, and python. Most of this new information was learned through extensive online research as well as inperson help from the faculty at tech. This research was essential to the completion of my subsystem because these were principles that became foundational to the design. Finally, a significant learning curve for this project was during my PCB design which was heavily informed by Dr. Pierce’s workshop. All these new areas came together to form the subsystem I ended up with and I am thrilled with the result. - Jim Camp
X. REFERENCES
[1] | “You | Breathe | the | Air | from | your
Crawlspace.” | Aquaguard | Foundation | Solutions.
https://www.aquaguard.net/resources/crawl-space-repair/yourbreathe-the-air-from-your-crawlspace/ (December 4, 2022).
[2] “Mold.” Center for Disease Control and Prevention. https://www.cdc.gov/mold/default.htm (December 4, 2022).
[3] | Shawn. | “Types | of | Distance | Sensors
and | How | to | Select | One?” | Seed | Studio.
https://www.seeedstudio.com/blog/2019/12/23/distancesensors-types-and-selection-guide/ (December 4, 2022).
[4] | Charlotte | Dorn. | “Creating | a | map | with | just
LIDAR | using | hector | slam.” | Charlotte | Dorn.
https://medium.com/@chardorn/creating-a-map-with-justlidar-using-hector-slam-231f3bab45e2 (December 4, 2022).
[5] | Brian | Bennett. | “This | is | why | your | Roomba’s
random patterns actually make perfect sense.” Cnet. https://www.cnet.com/home/kitchen-and-household/this-iswhy-your-roombas-random-patterns-actually-make-perfectsense/ (December 4, 2022).
[6] | Sachendra003. | “Arduino | - | Hu-
midity | Sensor.” | Arduino | Project | Hub.
https://create.arduino.cc/projecthub/sachendra003/arduinohumidity-sensor-288146 (December 4, 2022).
[7] | Limor | Fried. | “Thermistor.” | Adafruit.
https://learn.adafruit.com/thermistor (December 4, 2022).
[8] | ElectroPeak. | “Complete | Guide | to | Use | Soil
Moisture Sensor w/ Examples.” Arduino Project Hub. https://create.arduino.cc/projecthub/electropeak/completeguide-to-use-soil-moisture-sensor-w-examples-756b1f (December 4, 2022).
[9] TechSpaces. “A builder’s blueprint for construction technologies.” Home Innovation. The Closed Crawl Space:
Making the Transition (December 4, 2022).
[10] FCC. https://www.fcc.gov/Bureaus/EngineeringTechnology/Orders/2000/fcc00312.pdf (December 4, 2022).
[11] Superdroid. https://www.superdroidrobots.com/store/industries/pestcontrol/product=2729 (December 4, 2022).
[12] | Exr-2. | Robot: | https://exrobotics.global/robots/exr-2
(December 4, 2022).
[13] ROS. http://wiki.ros.org/ROS/Installation (December 4, 2022).
[14] Ubuntu. ttps://wiki.ubuntu.com/ (December 4, 2022).
[15] | ArduinoSPI. | https://wiki.seeedstudio.com/Software-
SPI/ (December 4, 2022).
[16] RaspberryPiSPI. http://www.penguintutor.com/electronics/rpiarduino-spi (December 4, 2022).

[17[ ArduinoSPIDaisyChain. https://forum.arduino.cc/t/spidaisy-chaining-nanos-to-a-mega/693424 (December 4, 2022).

[18] Turtlebot. https://www.robotis.us/turtlebot-3/ (December
4, 2022).
[19] Turtlebot E-Manual. https://emanual.robotis.com/docs/en/platform/turtlebot3/overview/(December 4, 2022).
[20] | Hackaday. | https://hackaday.io/project/167074-build-
your-own-turtlebot-3-backbone (December 4, 2022).
[21] HectorSLAM. http://wiki.ros.org/hectorslam (December 4, 2022).
[22] HectorSLAM. Github: https://github.com/tu-darmstadtros-pkg/hectorslam (December 4, 2022).
[23] | NFPA. | https://www.nfpa.org/codes-and-
standards/all-codes-and-standards/list-of-codes-andstandards/detail?code=70 (December 4, 2022).
[24] | IPC. | https://www.ipc.org/ipc-standards | (December
4, 2022).

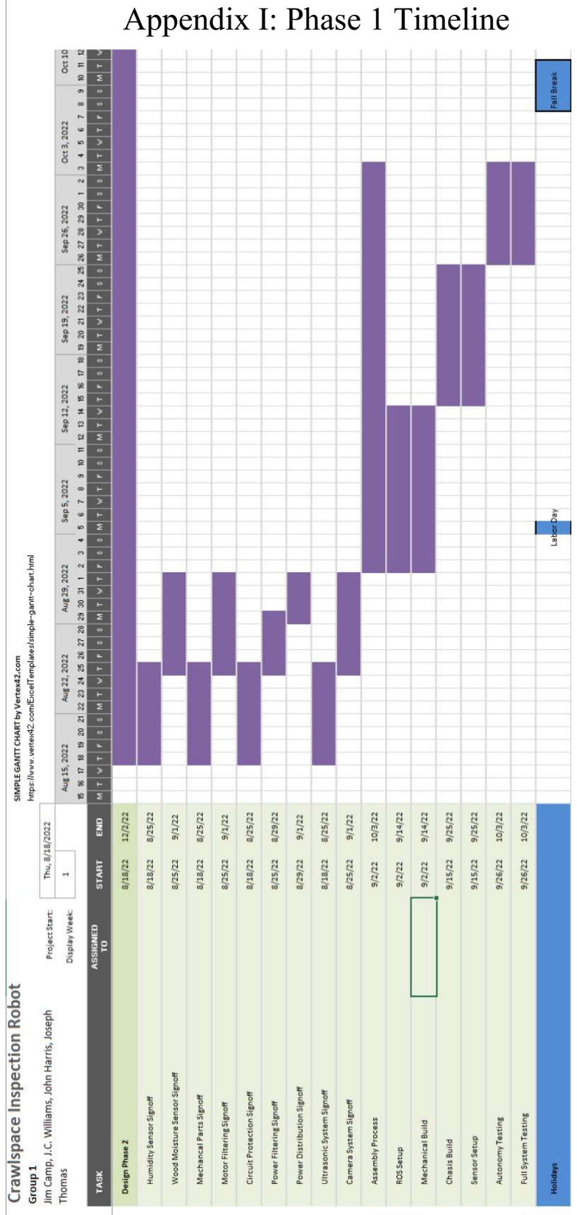
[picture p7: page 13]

Part Number | Description | System | Manufacturer | QTY | Unit Price | Total Cost | Required Purchased
12-Way Marine Fuse Block | 12V Fuse Box | Power | Docosu | 1 | $17.99 | $17.99 | YES
30 PCS Lever Wire Connectors Nuts Assortment Kit | Terminal Blocks | Power | XHF | 1 | $8.99 | $8.99 | YES
MUYI 2 Set Mini Blade Fuse Holder | Blade Fuse Holder | Power | Muyi | 1 | $7.99 | $7.99 | YES
MGI SpeedWare Latching Metal Toggle Switch | 2-Pin Swich | Power | MGI | 1 | $7.99 | $7.99 | YES
Micro USB Terminal | Micro USB Breakout Harness | Power | Poyiccot | 1 | $7.79 | $7.79 | YES
USB C Terminal | USB C Breakout Harness | Power | XMSJSIY | 1 | $7.50 | $7.50 | YES
ERJ-6ENF4321V | 4.32k Resistor | Power | Panasonic | 1 | $0.10 | $0.10 | YES
ERJ-6ENF1182V | 11.8k Resistor | Power | Panasonic | 1 | $0.10 | $0.10 | YES
ERJ-6ENF6342V | 63.4k Resistor | Power | Panasonic | 1 | $0.10 | $0.10 | YES
ERJ-6ENF4532V | 45.3k Resistor | Power | Panasonic | 1 | $0.10 | $0.10 | YES
ERJ-6ENF6982V | 69.8k Resistor | Power | Panasonic | 1 | $0.10 | $0.10 | YES
C2012C0G1H682J060AA | 6800 pF Capacitor | Power | TDK Corp | 2 | $0.22 | $0.44 | YES
08053C104JAZ2A | 0.1 µF Capacitor | Power | Kyocera | 1 | $0.34 | $0.34 | YES
CC0805JRNPO9BN120 | 12 pF Capacitor | Power | Yageo | 1 | $0.10 | $0.10 | YES
CL10A106MQ8NNNC | 10 µF Capacitor | Power | Samsung | 1 | $0.11 | $0.11 | YES
35SVPF22M | 22 µF Capacitor | Power | Panasonic | 1 | $1.45 | $1.45 | YES
GRM31CR61A476KE15L | 47 µF Capacitor | Power | Murata | 1 | $0.68 | $0.68 | YES
SDR1307-8R2ML | 8.2 µH Inductor | Power | Bourns Inc | 1 | $1.11 | $1.11 | YES
LM20343MH/NOPB | Buck Regulator | Power | Texas Instruments | 1 | $2.15 | $2.15 | YES
282837-2 | Terminal Block - Board Mount | Power | TE Connectivity | 2 | $0.99 | $1.98 | NO
L16-P | Linear Actuator | Enviromental Sensing | Actuonix | 1 | $80.00 | $80.00 | YES
PIND4E | Moisture Meter Probes | Enviromental Sensing | General Tools Store | 1 | $15.58 | $15.58 | YES
Arduino Nano 3 Pack | Atmega MCU | Enviromental Sensing | Arduino | 1 | $14.83 | $14.83 | YES
AT-K-C-26-6-B/7 | Spiral Cable | Enviromental Sensing | Assmann Components | 1 | $3.83 | $3.83 | YES
24316 Standoffs | | Enviromental Sensing | Keystone Electronics | 8 | $1.25 | $10.00 | YES
TBL009-254-08GY-2GY | Screw Terminal - 8 pin | Enviromental Sensing | CUI Devices | 1 | $2.11 | $2.11 | YES
TBL009-254-06GY-2GY | Screw Terminal - 6 pin | Enviromental Sensing | CUI Devices | 1 | $1.67 | $1.67 | YES
TBL009-254-02GY-2GY | Screw Terminal - 2pin | Enviromental Sensing | CUI Devices | 1 | $0.73 | $0.73 | YES
CC2D25S-SIP | Humidity Sensor | Enviromental Sensing | Amphenol | 1 | $19.23 | $19.23 | YES
1782 Temperature Sensor | | Enviromental Sensing | Adafruit | 1 | $4.95 | $4.95 | YES
SSA-103-W-T | Header Pins | Enviromental Sensing | Samtec | 3 | $0.54 | $1.62 | YES
93805A312 | M6 Threaded Rod, 18-8 Stainless Steel | Enviromental Sensing | McMaster-Carr | 1 | $9.12 | $9.12 | YES
2N3906 | MOSFET | Enviromental Sensing | Diotec | 5 | $0.05 | $0.26 | YES
C1206F104K5RACAUTO | Capacitor | Enviromental Sensing | Kemet | 1 | $0.49 | $0.49 | YES
RH73X2B10GKTN | Resistor | Enviromental Sensing | TE | 1 | $4.57 | $4.57 | YES
CRCW1206470MJPEAHR | Resistor | Enviromental Sensing | Vishay | 1 | $0.69 | $0.69 | YES
CRCW120647M0JPEAHR | Resistor | Enviromental Sensing | Vishay | 1 | $0.69 | $0.69 | YES
CR1206-FW-4704ELF | Resistor | Enviromental Sensing | Bourns | 1 | $0.10 | $0.10 | YES
CR1206-FX-8203ELF | Resistor | Enviromental Sensing | Bourns | 1 | $0.10 | $0.10 | YES
31:1 Metal Gearmotor 20Dx41L mm 12V CB | Motor | Enviromental Sensing | Pololu | 1 | $28.95 | $28.95 | YES
Pololu 20D mm Metal Gearmotor Bracket Pair | Mounting Bracket | Enviromental Sensing | Pololu | 1 | $6.95 | $6.95 | YES
637211 | Cascading X-Rail Slide Kit | Enviromental Sensing | Servocity | 1 | $122.99 | $122.99 | YES
L298N | Motor Driver Board | Enviromental Sensing | Qunqi | 1 | $6.99 | $6.99 | NO
XR-Y | Smart Robot Car Tank Chassis Kit | Movement | WiFi robot | 1 | $74.99 | $74.99 | YES
4845 | 47:1 Metal Gearmotor 25Dx67L mm HP 12V with 48 CPR Encoder | Movement | Pololu | 2 | $48.95 | $97.90 | YES
MD20A | 20A 6-30V DC Motor Driver | Movement | Cytron | 2 | $21.00 | $42.00 | YES
ABX00033 | Arduino Nano Every with Headers | Movement | Arduino | 1 | $15.00 | $15.00 | YES
Raspberry Pi 4 | ARM Microcomputer | Navigation | Raspberry Pi | 1 | $152.98 | $152.98 | NO
RPLIDAR A2 | 360 Degree Lidar | Navigation | Slamtec | 1 | $229.99 | $229.99 | NO
ZP-0110 | Rpi MCU Fan | Navigation | GeeekPi | 1 | $10.59 | $10.59 | YES
Ultrasonic Ranger 2.0 | Distance Sensor | Navigation | Grove-SeeedStudio | 4 | $4.30 | $17.20 | YES
TL-WR802N | WAP/WLAN Router | Navigation | TP-Link | 1 | $29.99 | $29.99 | YES
SVPro - HD USB Camera | HD Cam 60 Deg Lens | Navigation | SVPro | 1 | $60.99 | $60.99 | YES
HD USB Camera | HD USB Camera | Navigation | FiveBelow | 1 | $5.99 | $5.99 | YES
Emergency USB LED | USB LED 200 Lumens | Navigation | Voltaic Systems | 1 | $13.99 | $13.99 | YES

75 $763.23

### Appendix II: Full BOM and Budget

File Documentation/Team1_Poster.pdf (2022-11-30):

# Croomba: Autonomous Crawlspace Inspection Robot

## Joseph Thomas, John Harris, James Camp, and John-Caleb Williams

## Advisor: Jesse Roberts

# December 2022

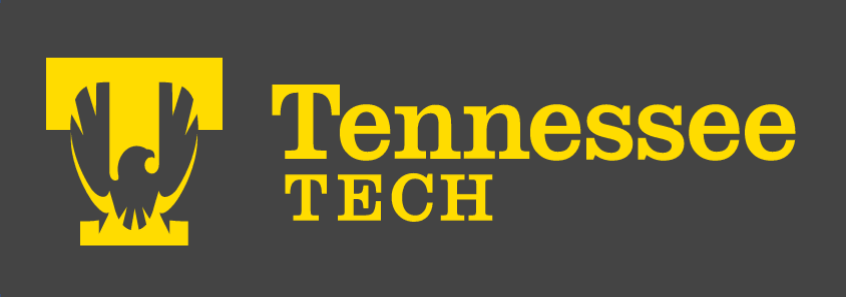
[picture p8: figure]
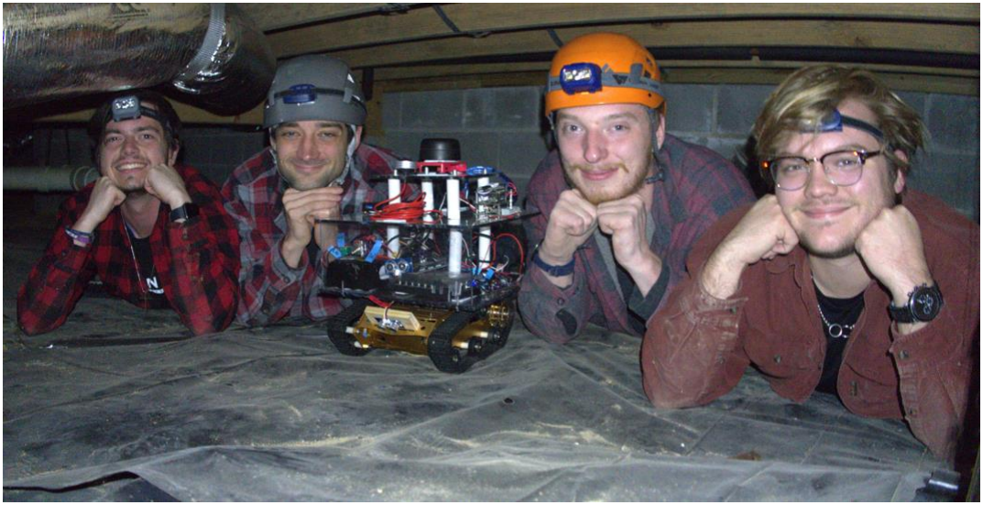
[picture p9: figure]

## Abstract

The final objective of the Croomba project is to create a robot capable of inspecting a crawlspace autonomously while also taking pictures and recording sensor data throughout. We have designed, ordered, and built the robot hardware while also setting up programs to demonstrate basic functionality.

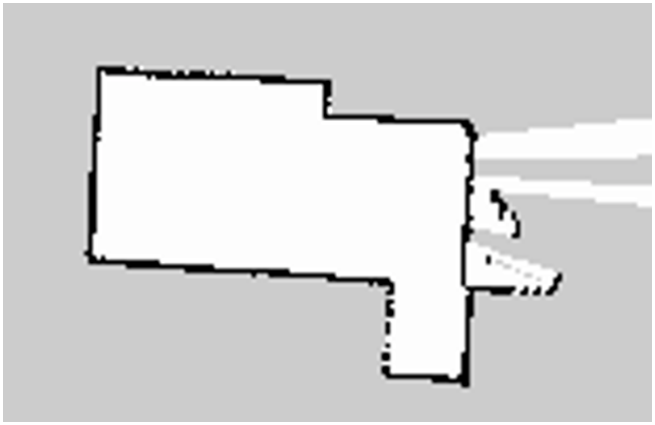
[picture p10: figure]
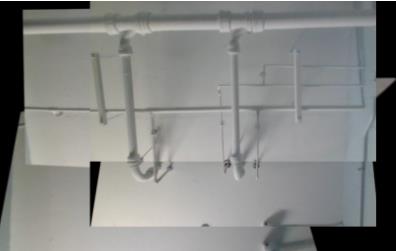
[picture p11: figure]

## Acknowledgments

The team would like to thank Jesse Roberts as well as the ECE faculty for their guidance and expertise. We would also like to give special thanks to Conrad Murray, Tristan Hill, Julie Mountain, Shellymar Repollet-Rodriguez, and the ME shop for their help.

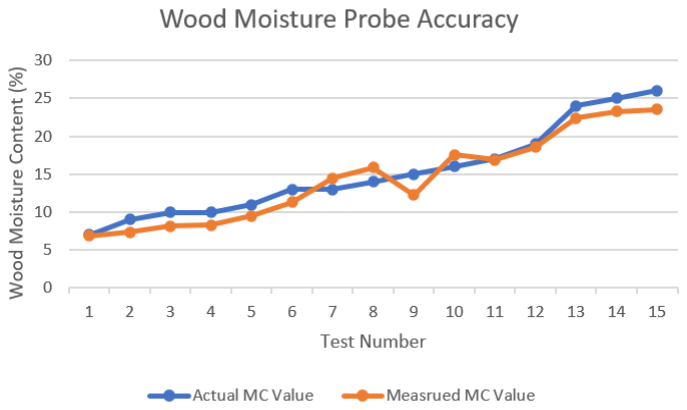
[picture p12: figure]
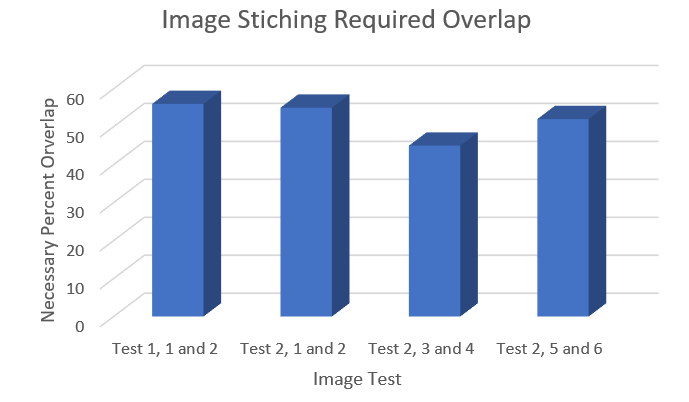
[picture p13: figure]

## Future Work

The modular nature of this project provides many opportunities for future work to be implemented on later iterations of the robot. Possible new features include upgrades to the hardware, a higher level of autonomy, improved chassis, and additional hardware for the sensing system. The image stitching algorithm will also be improved in future iterations. The Croomba will become a legacy project that future teams will continue to develop.

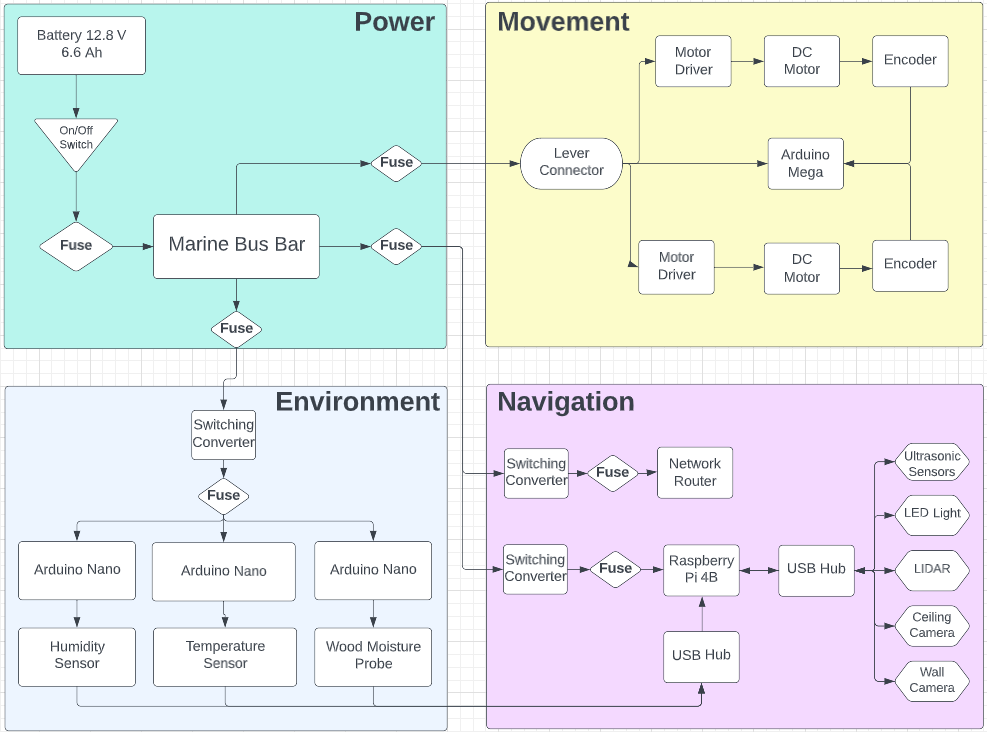
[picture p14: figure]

Navigation Capabilities
The navigation system includes a raspberry pi, a lidar, two cameras, and an array of ultrasonic sensors. It is currently capable of collision detection navigation, Hector SLAM mapping, and taking pictures at set intervals to enable image stitching.
Environmental Sensing Capabilities Humidity, temperature, and wood moisture content are all tested by this system. This data is then associated with a picture taken at the same time. Unfortunately, this subsystem's mechanical parts could not be physically realized due to ordering delays. Power Capabilities
The power system can safely provide 12V and 5V power to the system components as needed. The battery was found to provide around 1.5 hours of runtime.
Mechanical Capabilities
Although the mechanical design was not the project's focus, a chassis was assembled to allow all the electronic parts to be mounted. Motor encoders were also integrated into this system to allow for monitoring of the speed and direction of the motors.

## Mapping and Imaging

The implemented mapping and imaging algorithms allow the robot to survey its surrounding environment and record critical distance and environmental sensing information. The team utilized the Hector SLAM mapping algorithm, which was implemented in the Ubuntu-based Robot Operating System (ROS) environment. The Hector SLAM algorithm tracks changes in the robot's position and creates a two-dimensional map of the crawlspace environment. Through the Python-based library, OpenCV, the robot captures images of the ceiling and stitches them together into a single image. The resulting image allows users to monitor the health parameters of the subfloor.

## Experimentation

A variety of experiments were performed to determine the robot's functionality. Primarily, the team measured the robot's ability to accurately measure environmental data inside the crawlspace, how quickly the robot navigated the crawlspace, and the quality of the map and pictures that the robot formed as it maneuvered about the landscape.

## Industry Impact

Home inspections require a trained, licensed professional to spend valuable time moving through inhospitable, sometimes dangerous, environments. The Croomba has the potential to become an invaluable tool for the home inspection industry by automating the task of crawlspace inspection.

## Highlights

The Croomba was able to successfully map out a variety of different environments while navigating autonomously through the space. Base-level image stitching algorithms were implemented to create a holistic image of the area’s ceiling. While moving throughout the crawlspace, the robot collected sensor data to be visually represented on the stitched picture. Backup systems have also been implemented to allow the robot to be manually controlled in case of autonomy failure. Finally, the power system successfully filtered the supply to provide the constant voltages necessary for operation.

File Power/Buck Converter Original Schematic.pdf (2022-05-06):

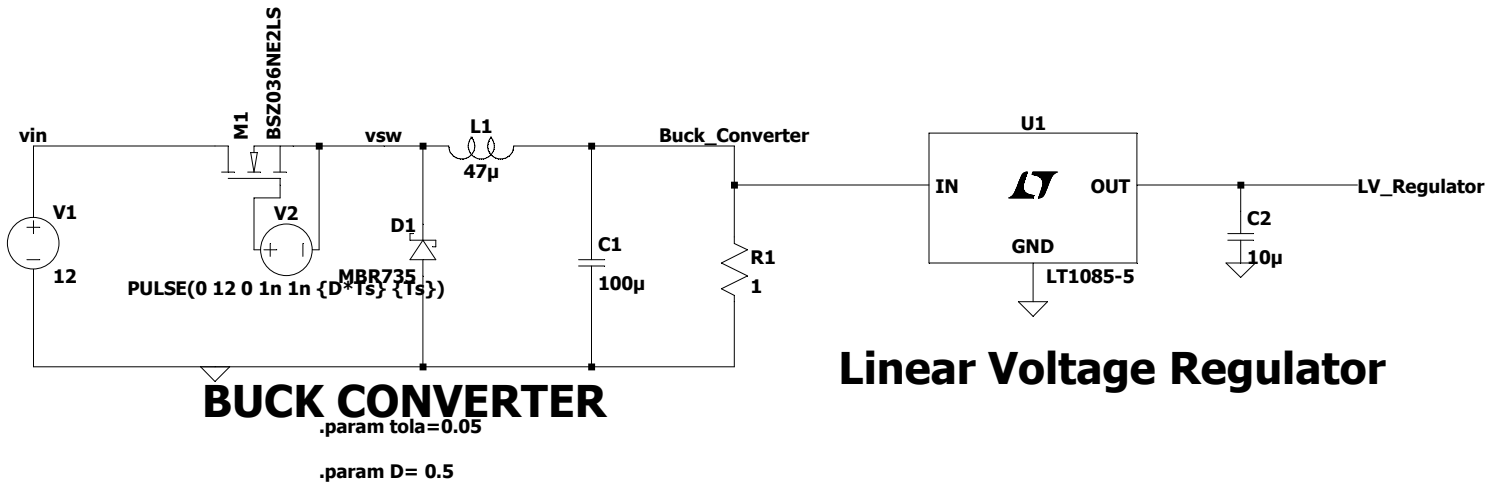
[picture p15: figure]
12 M¹ BSZ036NE2LS; PULSE(0 12 0 1n 1n {D*Ts} {Ts}); MBR735; GND; OUT; vin; vsw; Buck_Converter; LV_Regulator; .param tola=0.05; .param D= 0.5; BUCK CONVERTER; Linear Voltage Regulator

.param Ts = 10u
.tran 4m

## --- C:\Users\jimca\Downloads\Power\Power\power_second.asc ---

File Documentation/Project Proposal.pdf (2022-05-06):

# Autonomous Crawl Space Inspection Robot Project Proposal

James Camp, John-Caleb Williams, John Harris, Joseph Thomas
Electrical and Computer Engineering Department Tennessee Technological University Cookeville, TN
jrcamp42@tntech.edu, jawilliams46@tntech.edu, jharris44@tntech.edu, jwthomas43@tntech.edu
I. INTRODUCTION

Crawl spaces grant convenient access to the plumbing, duct work, and electrical wiring of a house, but they often present unique dangers to maintenance professionals and residents alike, such as exposure to harsh breathing conditions and hanging obstacles. Areas that are incredibly difficult for humans to reach can also present challenges for inspectors. This capstone project will focus on the design and assembly of a robot prototype that can perform these inspections autonomously while also providing sensor data to operators and homeowners. The end product will be an autonomous vehicle that is capable of traversing crawl spaces and recording conditions for operators and residents to review. An inspector will be able to drop the robot off at a client’s house and leave it there to collect the data freeing the operator up to work on other tasks. While navigating under the house, the robot will be constantly taking temperature and humidity data which allows users to see exactly what areas of the space will be prone to mold growth. A moisture probe will also be included to measure the moisture content of wooden beams found in a crawlspace. Members of the inspection industry stand to benefit greatly from this new product through its efficiency and convenience. Having a robot that can record inspection data without an operator present allows the time of company personnel to be spent on more important tasks. It also allows multiple people to look at the same data instead of only the people who went under the house seeing the information. An increased level of convenience is also provided. Not only is the operator no longer required to squeeze into a tight crawlspace, but the robot will also save all acquired data for the user to access at any time. In future iterations, a 3-dimensional model of the space will be created as well to create even more convenience. Inspectors stand to benefit greatly from the development of this robot.
The scope of the first iteration will include the ability to autonomously navigate through a simplistic crawl space with only a few obstacles present, collecting sensor data at certain intervals, and taking pictures that cover the majority of the crawl space perimeter. To prepare for future improvements the robot will also be outfitted with a receiver for manual control, although this may not be programmed within the time period. The sensor subsystem will be built with full modularity so that future iterations can replace the module with better sensors or new types of sensors. Other future improvements include continually improving autonomy and the ability to create a gradient of sensor data. The objective of this capstone project is to design a robot that will utilize optical and physical sensors that measure distance in order to navigate throughout a crawlspace environment, while simultaneously recording different environmental measurements including: humidity, temperature, and wood moisture levels.

II. FORMULATING THE PROBLEM

This section of the project proposal will introduce the required background information needed to make informed decisions about the project. This includes the industry standards we will be bound by when working on an engineering project. Specifications and constraints will also be detailed to narrow down the initial design parameters. Finally, a survey of the current solutions will be given to demonstrate where the product provides room for innovation and improvement.

A. Scientific Background

Much of the project’s importance lies within the scientific background associated with it. The scientific background also supplies the project with guidelines for the measurements and movement systems. The project will require background information in a variety of fields: biology, meteorology, and topography.
Fifty percent of the air that cycles through the first floor of a home comes from the crawl space, so the air quality and status of the crawl space’s climate has a direct impact on the air that the residents of the home intake [1]. If the crawl space is a humid, cool environment then mold will be extremely likely to grow in those areas. Mold causes a multitude of negative health effects for humans including stuffy nose, cough, red and irritated eyes, itchy skin rashes, fever, and shortness of breath [2]. The robot will be able to make autonomous measurements that a technician can use to determine whether or not mold is likely to grow in those spaces, and the pictures taken by the robot will ideally be able to show any mold that is growing within the space.

Every crawl space is different. Some spaces may have rocky, hilly terrain, whereas others may be flat but filled with puddles of standing water. With all of the different possible terrain that the robot may need to navigate, it is important that the robot be able to navigate in an ”all terrain” fashion or be suited for the average crawl space, which consists of a dirt floor and is decently level. In some circumstances, animals and pests may take up residence within a crawl space. It is not within the scope of the project to have any sort of extermination methods, but that would be a possibility for future groups.

B. Engineering Background

The objective of the autonomous crawl space inspection robot project is to develop a system that is capable of autonomously navigating, measuring sensor data, and moving throughout a crawl space environment.Navigation algorithms using optical and physical sensors as input information will be used, while simultaneously capturing images and recording humidity, moisture, and temperature measurements of the crawl space environment. As a mid-level autonomy device, operation will be performed without human interaction unless a critical error arises and human interference is needed in order to help the device succeed [3]. In order for the inspection robot to navigate autonomously throughout the crawl space, it will utilize measurements of optical and physical inputs from LIDAR, touch, and sound sensing.
A light detection and ranging (LIDAR) sensor is a device that fires a narrow, infrared, pulse of light, commonly referred to as a laser, from a transmitter terminal. The LIDAR sensor then utilizes a clock in order to track the time taken for the pulse to refract from an obstacle back to a receiver [4]. A LIDAR sensor is commonly mistaken with a non-laser, infrared (IR) sensor, which utilizes infrared light in order to detect when an emitted beam is broken, revealing that an obstruction is present and outputting an appropriate logic signal [4].
Physical sensors are another available option which can be used to alert a controller of possible obstructions. A Roomba, for example, is a device that utilizes a bump sensor that upon colliding with an obstruction, outputs a signal, alerting the controller that an object is in the way [5]. A trigger sensor is one example of a physical touch sensor which, upon colliding with an obstacle, will activate a trigger mechanism. This trigger mechanism will output a logic bit of one when a contact is pushed down onto the switch, and a logic bit of zero when a contact is no longer touching the switch [5].
Sound sensors, commonly referred to as ultrasonic sensors, utilize a clock, transmitter, and receiver in order to determine distance from an object. Ultrasonic sensors are able to determine the distance from an object by tracking the time taken for a transmitted sound wave to be received after reflecting off an object [4]. Since the crawl space inspection robot will be operating within an enclosed space, an algorithm could be developed that would determine the appropriate direction for the robot to move. By establishing an ultrasonic sensor on each side of the robot, a direction could be determined by computing which sensor had the longest time taken for a sound wave to be received. This algorithm would allow the robot to constantly move in a direction with the least amount of obstacles present.
By applying a combination of optical and physical sensors, a robot could achieve a higher level of accuracy for its autonomous navigation. One example is a higher level Roomba device, which utilizes an algorithm called Hector SLAM Mapping. Simultaneous Localization and Mapping (SLAM) is an algorithm which allows an object to mark data points whenever an obstacle is reached. The device will continue placing data points until enough points have been marked for the device to develop a map and navigate throughout a room [6]. By utilizing physical and optical sensors, a device could develop an even more accurate map of the environment and increase the efficiency of its navigation. An example of the SLAM algorithm, executed by a Roomba cleaning robot, is shown in figure 1 [7].

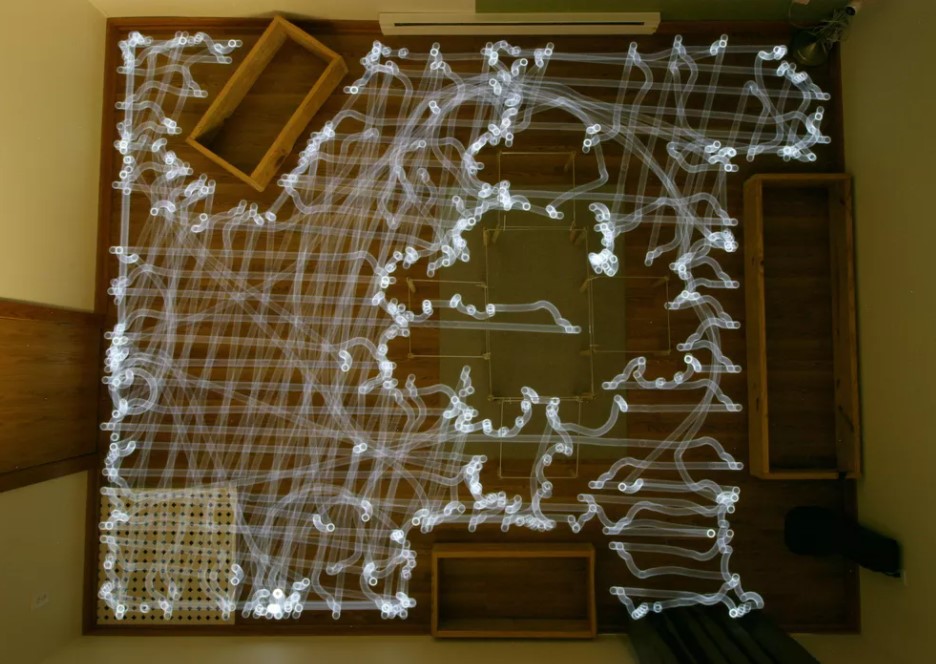
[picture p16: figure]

Figure 1: Hector Slam Mapping

In addition to autonomous movement, a foundation will be laid for a fail safe mechanism in which a human can intervene and operate the device manually, allowing for the device to return to its origin if an error arises. Radio controllers (RCs) are devices which utilize radio waves in order to transmit control signals to a device [8]. Through the use of a radio controller, commands could be sent from a transmitter on the manual controller to the receiver on the inspection robot. Additionally, with a camera mounted onto the inspection robots as well as a transmitter, video feed could be sent from the inspection robot to a receiver on the manual control. As outlined by the Federal Communications Commission (FCC), individuals without an amateur (HAM) radio license are legally allowed to transmit and receive control and video signals on specific bandwidths such as 27 MHz, 75 MHz, 2.4 GHz, as long as transmitter and receiver devices are properly certified for unlicensed use by the FCC [9].
Humidity, temperature, and moisture levels are relatively common measurements taken with module sensors designed for the Arduino microcontroller. The humidity of an environment is measured by applying an electric charge to a medium, placed between two electrode plates [10]. Depending on the level of resistivity, a humidity value can be determined, thus allowing the humidity of an environment to be measured with a typical accuracy of five percent. Additionally, the temperature of an environment can be measured through the use of a thermistor, a resistor device whose resistance value has a direct, linear relationship to temperature [11]. Moisture levels are commonly measured in the same context as humidity levels. In order to measure moisture level, two probes are placed into a material or space and an electric pulse is sent between the probes of the device. The resulting resistance is measured and then a correlated moisture level can be determined [12].
The proposed power system for this inspection robot would utilize cordless drill batteries as voltage sources. Cordless drill batteries can allow for modular application and ease of use due to the batteries being easily removed and replaced with charged versions should they fail. These cordless drill batteries would need to be utilized with specific adapters due to connectivity constraints, shown in figure 2 [13]. The suggested battery adapters will have fuses and kill switches built in or added by the team in order to ensure that safety voltages are not exceeded, and allow for a manual kill switch if necessary. Most cordless drill models come with LED indicators built in so that power level can be observed. Circuit options for reducing voltages for various components will be carried out with voltage dividers, and Zener diodes can be used to ensure the safety of microprocessor components. The team believes one 20 V battery might be sufficient for the power system of the crawl space inspection robot, however, if necessary, a second battery may be added in parallel to increase operating time.

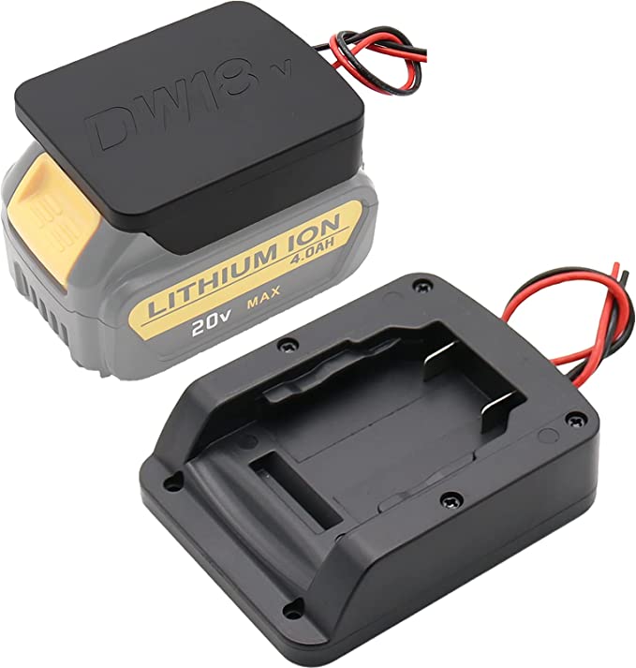
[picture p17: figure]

Figure 2: Battery Adapter

C. Constraints

The crawl space inspection robot must adhere to certain constraints in order to be deemed appropriate and properly designed. The average height of the crawlspace of a home ranges from 44 to 48 inches but can often be much smaller [14]. This will create a limit how tall the robot can be in order to serve the maximum number of households. All components and wiring within the chassis must also be properly protected and sealed from water and dust exposure as these elements will be plentiful in most crawlspaces.
The chosen power system of the device must be able to supply the different voltage requirements of various components within the system, such as 12 Volt motors and 5 Volt controllers. It is also important that it can provide power long enough for the entire crawl space to be explored. Because a foundation will be laid for manual control through the implementation of transmission and receiving hardware, constraints will be placed on what frequencies can be used as well as the device range. The receiver and transmitter must be able to operate only on frequency channels which do not require an amateur license, like 27MHz, 75 MHz, and 2.4 GHz [9].
D. Specifications

The crawl space inspection robot must adhere to certain specifications in order to achieve the desired objectives. First, the device must be shorter than 16 inches, or two blocks, to allow practical utilization of the device in almost any home. However, because crawl spaces can be 44-48 inches [14], the moisture probe will be able to extend at least 32 inches from the top of the chassis allowing it to fit in most spaces while also reaching most wooden beams. As for the other sensors, because small sensors can often have accuracy problems, at least two temperature and two humidity sensors will be included to compare values and ensure accuracy in the measurements. This will not be the case for the wood moisture probe as that sensor will be custom built. To ensure its accuracy, feedback sensors will be added to the arm to ensure the probe is applied with the correct pressure at all heights. This ensures that the measurement will be accurate and consistent in most crawl spaces.
The batteries chosen must allow for the system to operate at minimum of four hours which should provide sufficient time to navigate the space. All parts, including the battery and sensors, will be picked with heavy consideration on environmental ratings to prevent parts from wearing out due to dust, dirt, or moisture. For this reason, the battery will not have any exposed electrical contact points during operation. This specification will prevent rust and deterioration of the contacts from limiting the battery’s performance.
E. Standards

It is vitally important for the team to understand the standards put in place by the government and engineering societies because they act as restrictions and guidelines for the design of the robot. The IEEE sections 1872.2-2021 and 7007-2021 on autonomous robots and ethically driven robots and automation as well as the NEC within the NFPA in particular will have the greatest effect on the robot. The team will need to be familiar with the content of the above standards in order to create a product that adheres to the code of conduct specified in those standards.
For example, Article 310.10.C of the NEC states that insulated conductors and cables used in wet locations shall be moisture impervious or metal-sheathed or be of a type listed for use in wet conditions. Furthermore, section 310.14 contains the requirements for Ampacities for conductors rated 0-2000 Volts [15]. The constraints described in these sections and others will have a direct impact on the design of the Autonomous Crawl Space Inspection Robot.
Along with the design, the assembly of the first prototype will also have to follow industry standards. IPC sets international standards regarding the assembly of everything from soldering to Printed circuit boards (PCBs). Because this product will need to have a long lifecycle but does not perform any health or safety-critical operations, it will be classified as an IPC class 2 product. One member of the group holds an active certification in IPC-J-STD-001 and will be responsible for inspecting all soldering and PCB assembly to ensure compliance to the standard.
F. Survey of Possible Solutions

There are currently inspection robots available which can accomplish a variety of feats and assist individuals in the inspection of different environments such as crawl spaces. For example, one inspection robot currently available is the GPK-32 Wireless Robot from SuperDroid Robots that is capable of capturing high resolution video for inspection through manual operation [16]. Additionally, another available inspection robot is the autonomous ExR-2 from Energy Robotics which is capable of autonomously navigating through a hard environment in order to provide video footage [17].
A major benefit over the existing robots is the addition of the sensor module. This module allows the robot to make the recordings an inspector would have to manually make otherwise. The module allows the ability to record more points and display the recorded data overlaid with a map of the crawlspace. This gives operators more information and presents it in a more useful and aesthetic way than plain numbers.
Another piece of technology utilized by the inspection and crawl space industry is a wood moisture probe which shows how much moisture is in the wooden boards underneath a house. In order to get moisture measurements from wooden boards, a person must manually push the probes into a board. The team’s robot will be able to perform this action autonomously which saves the operator from having any need to go underneath a crawlspace in the vast majority of cases. While there are currently solutions which exist and are available for purchase, the cost of these solutions are high, ranging from thousands to tens of thousands of dollars. There does not appear to be an affordable inspection robot that can meet all required specifications given for this autonomous crawl space inspection robot.
G. Summary of the Problem
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

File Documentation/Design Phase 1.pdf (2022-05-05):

# Team 1 Design Phase 1

James Camp, John-Caleb Williams, John Harris, Joseph Thomas
Electrical and Computer Engineering Department Tennessee Technological University Cookeville, TN
jrcamp42@tntech.edu, jawilliams46@tntech.edu, jharris44@tntech.edu, jwthomas43@tntech.edu
I. INTRODUCTION

In Design Phase 1, the team began to formulate a high-level design of the autonomous crawl space inspection robot. This included an atomic block diagram of the overall system along with a schedule of tasks. Preliminary ideas for each subsystem’s detailed design were also generated during this phase along with justifications describing why the decisions were made. The Design Phase 1 process also allows team members to begin to break their design into atomic subsystems and to formulate possible relationships between each of the subsystems. In the block diagram, the information being
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

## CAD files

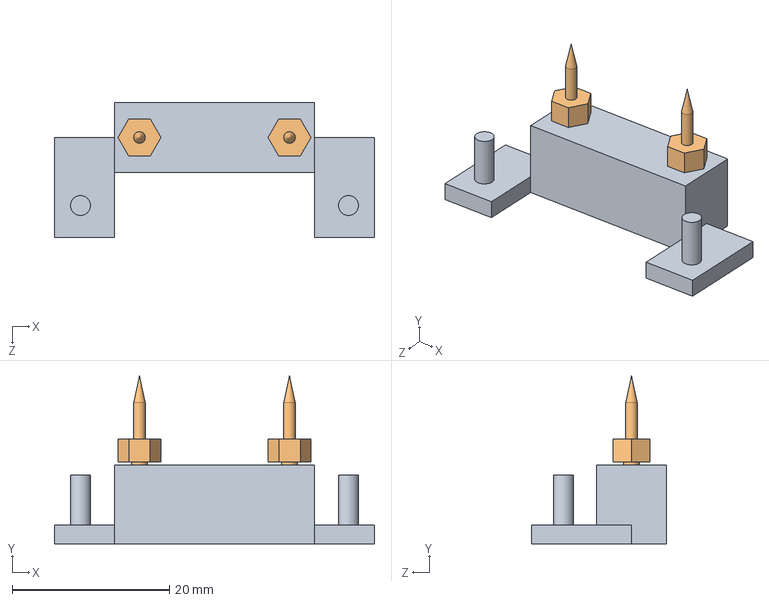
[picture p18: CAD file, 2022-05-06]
Environmental Sensing/Models/Head_Assembly.SLDASM
40.6 x 21.3 x 17.1 mm
Probe_Head
Probe x 2

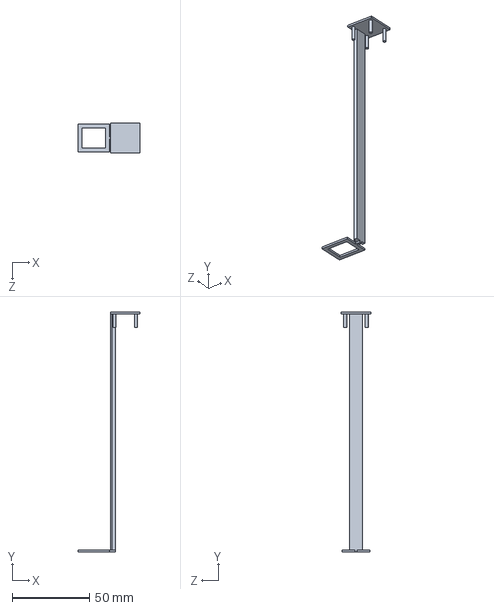
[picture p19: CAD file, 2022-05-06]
Environmental Sensing/Models/Bracket.SLDPRT
40.1 x 154.9 x 19.0 mm

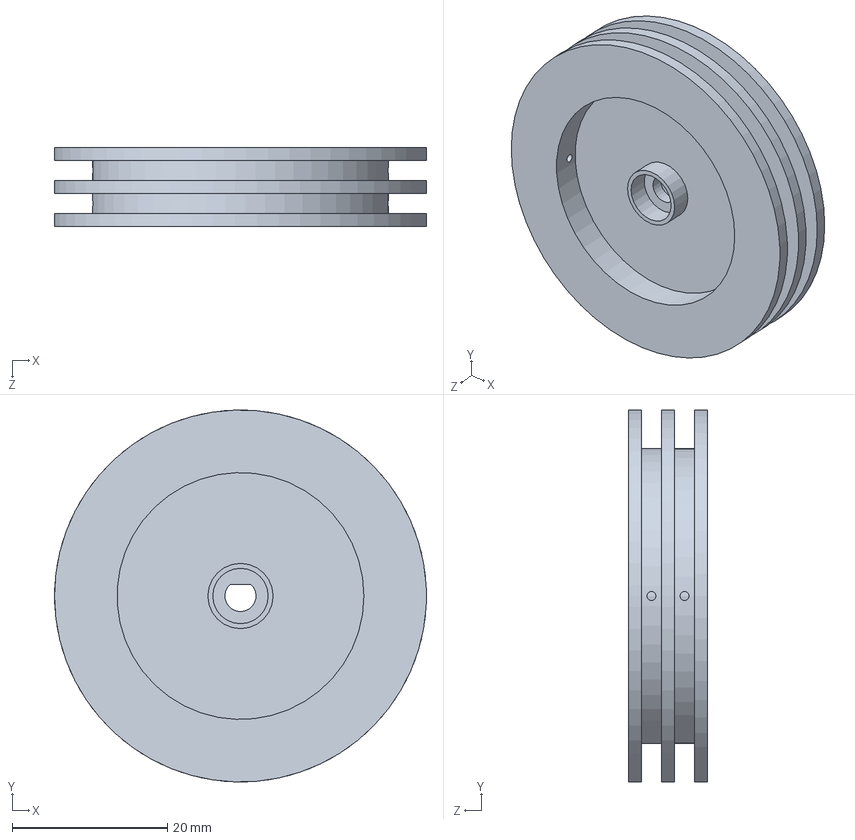
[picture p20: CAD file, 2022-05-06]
Environmental Sensing/Models/Pulley.SLDPRT
47.9 x 47.8 x 10.2 mm

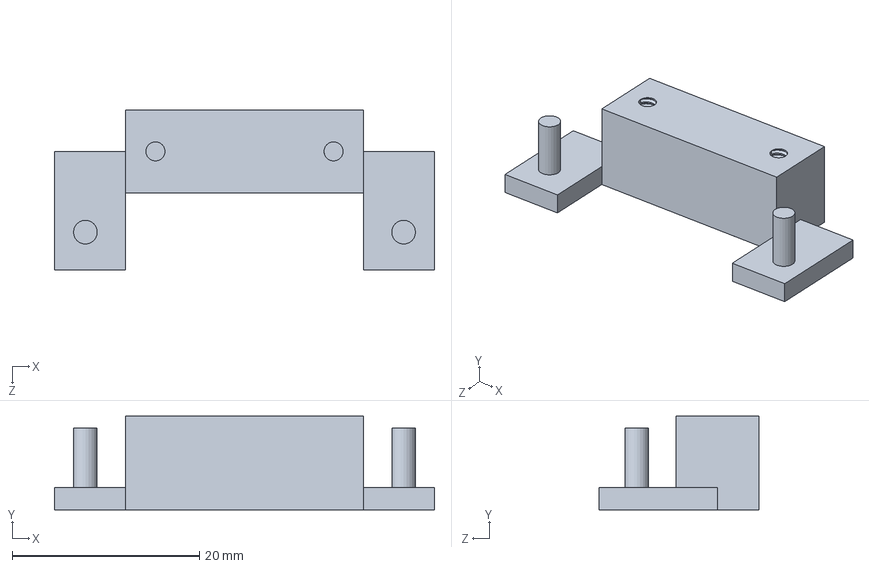
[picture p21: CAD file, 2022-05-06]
Environmental Sensing/Models/Probe_Head.SLDPRT
40.6 x 10.0 x 17.1 mm

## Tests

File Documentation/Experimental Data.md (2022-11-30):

# Croomba Experimental Data
## System Testing

## Power
In order to verify the power subsystem is meeting all requirements, 5 trial runs measuring the voltage and current of each main subline coming off the battery were carried out, and the results are in the tables below. We ran over an hour and fifteen minutes of trial runs while programming. The power system successfully powered all subsystems without outside assistance. This proves the two constraints laid out in the proposal that the power subsystem will provide correct current and voltage to the subsystems for a time that would allow mapping of a crawlspace environment.  
### Main Power LN 2 & 5
Trial Number (N)|Current(A) | Voltage (V)  |
|:---: | :---:|:----:|
| 1 |       0.526 A |        13.26 V|
| 2 |       0.627 A |        13.26 V|
| 3 |       0.675 A |        12.85 V|
| 4 |       1.265 A |        12.68 V|
| 5 |       1.326 A |        12.75 V|

### Navigation LN 7A & 8A
Trial Number (N)|Current(A) | Voltage (V)  |
|:---: | :---:|:----:|
| 1 |       0.7 A |    5.33 V|
| 2 |      0.6 A |       5.34 V|
| 3 |      0.79 A |       5.33 V|
| 4 |       0.7 A |        12.68 V|
| 5 |       1.326 A |        12.75 V|

### Network Router LN 9A & 10A
Trial Number (N)|Current(A) | Voltage (V)  | 
|:---: | :---:|:----:|
| 1 |      0.1 A |       5.3 V|
| 2 |      0.12 A |       5.32 V|
| 3 |       0.12 A |       5.31 V|
| 4 |       0.28 A |        5.31 V|
| 5 |       0.33 A |        5.3 V|

### Movement LN 11A & 12A
Trial Number (N)|Current(A) | Voltage (V)  | 
|:---: | :---:|:----:|
| 1 |       0.526 A |        13.26 V|
| 2 |       0.627 A |        13.26 V|
| 3 |       0.675 A |        12.85 V|
| 4 |       1.265 A |        12.68 V|
| 5 |       1.326 A |        12.75 V|

### Environmental Sensing  LN 13A & 14A
Trial Number (N)|Current(A) | Voltage (V)  | 
|:---: | :---:|:----:|
| 1 |      0.0642 A |       5.24 V|
| 2 |       0.0645 A |       5.23 V|
| 3 |       0.0644 AA |       5.26 V|
| 4 |       0.0.065 A |        5.31 V|
| 5 |       0.064 A |        5.3 V|

###

## Navigation

### The Model Crawlspace

To test the navigation functionality of the autonomous crawlspace inspection robot, a rectangular-shaped model crawlspace was created, with a length of 16.5 ft, a width of 6 ft, and a resulting area of 99 square feet. Floor tiles were used as a reference for quantifying the crawlspace area, with each floor tile having an area of 9 in by 9 in. The walls of the model crawlspace were made with various materials available in the laboratory and had a minimum height of 17 in and a maximum height of 36 in. 

### Mapping
The main job of the system's lidar is to create a map of the surrounding area without having to be provided a manually drawn map by the operator. To ensure that the map is being generated correctly, the perimeter of our test area was found by measuring the picture at a set zoom and creating a proportion from that value, and the percent error was calculated. The areas missed were then measured on the screen and the proportional value was applied to convert into the physical distance. The focus of this experiment was to identify the areas along the perimeter that the lidar missed as the additional points it caught past the perimeter are blocked by the true wall. 

| Perimeter (ft) | Measured Perimeter (ft) | Percent Error (%) |
| :---: | :---: | :---: |
| 47.75 | 45.74 | 4.39 |
| 41 | 38.63 | 6.14 |
| 41 | 38.68 | 6.00 |

The results show that the lidar was able to successfully map the majority of the perimeter as it navigated throughout the crawlspace. In the worst case, the robot only failed to map 6.14% of the model environment. However, this percentage should be mostly negligible because none of the gaps in the walls of the model crawlspace are large enough for the robot to fit through. 



### Maneuvering 
In adherence to movement specifications, the robot needs to be capable of maneuvering through 70 % of the model crawlspace. To test adherence to this requirement, the team members counted which of the floor tiles in the model crawlspace the robot had not touched, and therefore how much of the total area of the crawlspace the robot had not maneuvered through. Additionally, the robot was initially placed in different corners of the model crawlspace to test the behavior from different initial positions. 

In this experiment, the total area of the crawlspace was roughly 100 square feet and the total area covered by the robot is calculated and listed, along with the total percentage of the crawlspace area covered during the test. It is worth noting that in addition to the area listed in the table below, the robot often crossed back through past squares, effectively increasing the total area covered by the robot. 

| Area Where Present (ft^2) | Percent of Area Covered (%) |
| :---: | :---: |
| 86.50 | 86.50 | 
| 91.00 | 91.00 | 
| 82.00 | 82.00 | 
| 76.38 | 76.38 |
| 85.94 | 85.94 |

As shown in the above table, the crawlspace inspection robot was able to maneuver through more than 70 % of the model crawlspace area, often maneuvering through more than 80 % of the space without getting stuck or needing assistance from the operator. It is important to note that while the robot did not enter 100 % of the tiles in the crawlspace area, not every tile must be entered for an incredibly detailed map to be created within the ROS software using the LiDAR sensor.  

### Imaging Quantity
After adjusting the project's scope, imaging has been reprioritized and will take precedence over autonomous control. Because we plan to stitch the images of the crawlspace together using python and OpenCV, it is essential to test what percentage of the ceiling we can successfully photograph. We tested this metric by treating the photographs taken as a jigsaw and then finding the area of any spots not recorded and comparing that area to the overall ceiling area.

| Total Ceiling Area (ft^2) | Pictures Taken | Area Pictured (ft^2) |
| :---: | :---: | :---: |
| 87 | 33 | 7920 |
| 87 | 36 | 8640 |
| 87 | 54 | 12960 |
| 87 | 51 | 12240 |
| 87 | 42 | 10080 |

After allowing the robot to run its course, the number of pictures taken can be seen in the table above. The real area captured by each picture was then multiplied by the number of pictures taken to find a value for the full area pictured. While this value will feature some overlap, it is significantly large enough to convince the team that the robot saves pictures that will cover the entire ceiling area. Along with this metric, the photos were flipped through and ceiling landmarks were used to confirm that no part of the ceiling was missed.

### Imaging Quality
Python code was created using the OpenCV library to perform the image stitching. This test was performed using both real pictures taken of the ceiling using the robot's camera and pictures of a crawlspace ceiling. This allows us to confirm that the code will work both in a real crawlspace setting and will also work when using the camera. 

| Compared Pictures | Percent Overlap (%) |
| --- | --- |
| Test 1, 1 and 2 | 56 |
| Test 2, 1 and 2 | 55 |
| Test 2, 3 and 4 | 45 |
| Test 2, 5 and 6 | 52 |

Tests were performed on the pictures taken to find the necessary overlap percentage between pictures. It was found that this overlap was around 50% for all the stitchings that worked correctly.



### Wireless Access Point
The main job of the system's wireless access point is to create a wireless network for communication between the system's main control, the Raspberry Pi, and the system operator in the case that manual control is needed. Adhering to the given constraints, the wireless access point operates on 2.4 GHz and is a private network that requires a password for use. To ensure that the wireless access point was sufficient for use, the distance and overall connectivity, and control were tested four times.  

In each of the four tests, a laptop was connected to the Raspberry Pi at a distance of 100 feet, first on the fourth floor of Brown Hall and then on the third floor of Brown Hall. The robot was pinged by the laptop with 32 bytes of information, and the response time in milliseconds from the computer to the Raspberry Pi and back was recorded. Finally, the overall system control was tested by opening applications and interacting with the system peripherals such as one of the USB cameras over Microsoft Windows Remote Desktop Protocol. 

| Distance From Robot (ft) | Average Ping Time (ms)| Full Desktop Control? |
| :---: | :---: | :---: |
| 100 | 4 | Yes |
| 100 | 3 | Yes |
| 100 | 3 | Yes |
| 100 | 3 | Yes |

The results show that the wireless access point is sufficient for the application of the crawlspace inspection robot and that operators will be able to successfully control the robot from well over 70 feet away, allowing for manual control in more significant than average home crawlspaces, which would only require a max communication distance of 70 feet.   

## Environmental Sensing
### Temperature
The sensor was placed outside at different times and compared to the ambient temperature given by Weather.com. The test was performed like this because the commercially available sensor turned out to be incredibly slow and inaccurate. It was also done in this way because an outdoor environment is where the robot will be used. 
| Date/Time Recorded | System Temperature Sensor (°F) | Website Listed Temperature (°F) | Percent Error (%) | Difference (°F) |
| :---: | :---: | :---: | :---: | :---: |
| 11/5/2022 23:30 | 62.825 | 63 | 0.28 | 0.175 |
| 11/6/2022 0:44 | 61.5375 | 61 | 0.88 | 0.5375 |
| 11/6/2022 1:23 | 57.925 | 59 | 1.82 | 1.075 |
| 11/6/2022 11:53 | 62.2375 | 64 | 2.75 | 1.7625 |
| 11/6/2022 15:06 | 71.125 | 70 | 1.61 | 1.125 |
| 11/6/2022 16:33 | 66.6875 | 67 | 0.47 | 0.3125 |
| 11/6/2022 21:46 | 66.5375 | 64 | 3.96 | 2.5375 |
| 11/7/2022 17:40 | 65.53 | 66 | 0.71 | 0.47 | 

The table shows that the system temperature sensor has exceptional accuracy when compared to a purchased sensor. The max error found was just under 4% which is well within the level of accuracy which we were hoping for.
### Humidity
The sensor was placed outside at different times and compared to the humidity given by Weather.com. The test was performed like this because the commercially available sensor turned out to be incredibly slow and inaccurate. It was also done in this way because an outdoor environment is where the robot will be used. 
| Date/Time Recorded | System Humidity Sensor (%RH) | Website Listed Humidtiy (%RH) | Percent Error (%) | Difference (%RH) |
| :---: | :---: | :---: | :---: | :---: |
| 11/5/2022 23:30 | 82.3 | 84 | 2.02 | 1.7 |
| 11/6/2022 0:44 | 87.1 | 89 | 2.13 | 1.9 |
| 11/6/2022 1:23 | 93.1 | 95 | 2.00 | 1.9 |
| 11/6/2022 11:53 | 86.9 | 86 | 1.05 | 0.9 |
| 11/6/2022 15:06 | 83.2 | 84 | 0.95 | 0.8 |
| 11/6/2022 16:33 | 95.4 | 99 | 3.64 | 3.6 |
| 11/6/2022 21:46 | 92.8 | 96 | 3.33 | 3.2 |
| 11/7/2022 17:40 | 37.5 | 38 | 1.32 | 0.5 |

The table shows that the humidity sensor is well within our desired range for accuracy. The datasheet for the DHT22 sensor says the accuracy should be ±2 %RH. While this experiment found several points outside this range, it seems to mainly be at the higher humidity values where the accuracy decreases. However, even at these points, the accuracy is at a very acceptable level.  

### Moisture Content
The Moisture Probe was first tested using axial resistors so that a known value could be tested. The resistors were also checked on a multimeter so that the true value could be compared along with the listed value. This test provided limited results due to the availability of resistors to test. However, it is secondary to the full moisture content testing and was mostly used for troubleshooting.
| Known Resistance (MΩ) | Multimeter Result (MΩ) | Probe Result (MΩ) |
| :---: | :----: | :----: |
| 1 | 1.02 | 1.02 |
| 2.2 | 2.23 | 2.23 |
| 4.7 | 4.83 | 4.82 |
| 10 | 9.88 | 9.78 |
| 47 | 51.0 | 46.0 |

The results above were all found to be accurate within 1% error except for the 47 MΩ test which had about 10% error. This is because it was found that the first two stages had greatly increased accuracy compared to the stages with larger resistors used in the voltage divider. After much research, it was found that Arduino analog read pins prefer a smaller input impedance which was unknown at the time of design. This could be fixed in future revisions by switching out the microcontroller used. 

The system was used on blocks of wood with differing moisture contents and compared to the results given by a commercial wood moisture probe. Forcing a piece of wood to be a certain moisture content caused some problems with this experimentation. Leaving the wood pieces in a steamy room allowed values between 7% and 11% to be tested but the higher values could not be achieved this way.  Instead, a piece of wood was soaked with water and tested at different times as the wood dried out and its moisture content fell. This allowed the higher values to be tested.
| COTS Moisture Content Probe | System Moisture Content Probe | 
| :---: | :----: |
| 7 | 6.86 |
| 9 | 7.34 |
| 10 | 8.13 |
| 10 | 8.31 |
| 11 | 9.51 |
| 13 | 11.31 |
| 13 | 14.44 |
| 14 | 15.89 |
| 15 | 12.26 |
| 16 | 17.55 |
| 17 | 16.87 |
| 19 | 18.55 |
| 24 | 22.4 |
| 25 | 23.26 |
| 26 | 23.54 |

As can be seen from the table above, the actual moisture content value is not 100% accurate for the commercial probe. However, all values fall within ±3 of the expected percentage value. The collected data shows that the system is detecting changes within the moisture content of the plank. Based on the raw resistance values which were seen in the previous section. It is believed some of this error comes from the equation created to convert resistance to wood moisture percentage. 

## Movement
### The Height Constraint
For the first test, we measured the height of the robot with a tape measure. This was done to ensure that the 16-inch height constraint was met. This experiment was conducted twice and the results are displayed below. 
| Trial Number | Height of Robot |
|:---: | :---: |
| 1 | 15.1875 inches  |
| 2 | 15.1875 inches  |

The above results show that the robot is 15.1875 inches tall. That number is less than 16 inches, and thus the height constraint has been met.
### Motor Encoders
The purpose of this test is to confirm that the motor encoders and Arduino software are correctly measuring the rotational speed of the motors. The motor encoders are connected to GPIO pins on the Arduino, and the software reads the frequency of the signals and converts them into a rotational speed that is displayed on the serial monitor. Those values were compared against a measurement obtained by using a digital tachometer placed in contact with the drive wheel. The values in the table below are in units of RPMs.
|Robot's Reading|Tachometer Reading|Percent Error|
|:---: |:---: |:---: |
|219.7 |220 |0.136% |
|218.5 |219.2 |0.319% |
|220.1 |219.8 |0.136% |
|219.2 |219.9 |0.319% |
|220 |220.6 |0.272% |

These results show that the Arduino program for the motor encoders is correctly measuring its speed.
### Linear Speed
For this experiment, the team wanted to measure the robot’s linear speed. The desired speed is about 1 foot per second.  To do this, we measured out 10 feet with a tape measure and then used a stopwatch to determine how quickly the robot covered that distance. This gives us the average velocity of the robot. 

The measured values for average velocity were also compared to the instantaneous RPMs that were displayed in the Arduino Serial Monitor while the robot was in motion. Those values were recorded and are displayed below. The RPMs are also converted to feet/second for ease of comparison.
|Travel Time|Average Speed(ft/s)|Instant. Speed(RPMs)|Instant. Speed(ft/s)|Percent Error|
|:---: |:---: |:---: |:---: |:---: |
|9.75 |1.03 |138.7 |1.09 |5.505% |
|9.68 |1.04 |135.8 |1.07 |3.21% |
|9.71 |1.03 |137.8 |1.088 |5.331% |

These results show that the average speed of the Croomba is about 1 foot per second which is the desired value. 
### 30 Degree Incline
Finally, a test was done to determine whether or not the Croomba could ascend a 30-degree inclined plane as described in the signoffs. To accomplish this, the team put together some pieces of plywood at a 30-degree angle and set the Croomba on a course to see if it could make its way up the hill. This test was conducted 3 times.

The Croomba was unable to go up the steep slope. The team believes this deviation is caused by a lack of traction on the treads as well as a high center of mass on the robot. That high center of mass pulls the robot back down the hill and the front of the bot begins to lose traction with the ramp. In short, the robot is too top and back heavy, and this leads to the robot wanting to flip onto its back like a turtle when ascending the incline. 

However, the team conducted additional experiments by lowering the angle of the incline to find the maximum angle that the robot could traverse. All of the results are displayed in the table below.
| Incline Angle | Croomba Ascension? |
|:---: | :---: |
| 30 | No |
| 30 | No |
| 30 | No |
| 25 | No |
| 20 | No |
| 15 | Yes! |
| 15 | Yes! |

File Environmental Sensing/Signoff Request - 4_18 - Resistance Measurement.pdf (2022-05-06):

The original direction of the moisture probe circuit had to be changed because the normal resistance values of the wood being tested were much bigger than expected and had a much larger range going from about 460 kΩ to 22,400 MΩ [1]. This caused the current mirror to stop working effectively because even when the bias resistor had its value raised the range was too large and significant variations in current occurred. Analysis of this issue was performed in LT Spice and is found in figures 1 and 2.

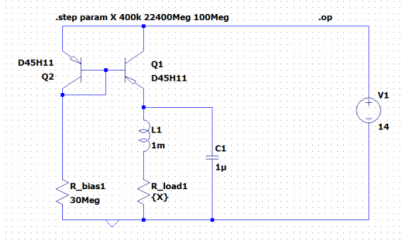
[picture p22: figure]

Figure 1: Current Mirror Schematic

Figure 2: Current Mirror Step Analysis, Resistance (Ω) vs Current (Amps)

Multiple methods were experimented with to fix this issue with the first being a constant current IC to provide a known current value independent of the test resistor. However, this method was found to not work due to the wide range of resistance values. At a constant current which provides a reasonable voltage reading at the low resistance value, the high resistance value returns an excessively large current.

A second method was tested using a modified voltage divider and an MCU with an onboard voltmeter. Through a woodworking webpage, data was found showing a way to hook up a voltmeter with a known voltage, as seen in figure 3, and use some calculations with the internal resistance to solve for the probe resistance [2]. The equation is

which is obviously a rearranged version of the voltage divison equation. The plan was to preform this method with a multimeter board called a click. However, no multimeter of that form factor had the necessary resolution for this wide a range

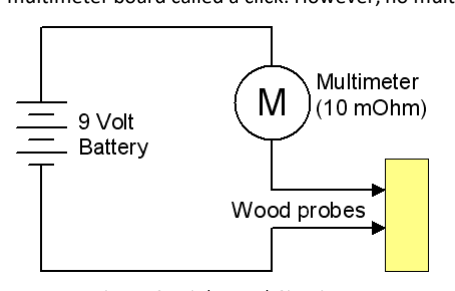
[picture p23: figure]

Figure 3: High-Level Circuit

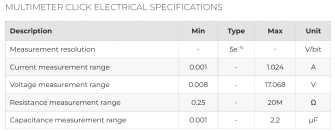
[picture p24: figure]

Figure 4: Click Specs

All this research left the only option being an auto-ranging ohmmeter which uses a voltage divider. Although I was initially advised away from this option, opening a COTs wood moisture probe and inspecting revealed that this is how they approach that problem as well. The main issue that normally arises with voltage divider measurements is that care has to be taken in choosing resistors for R1 that have a low tolerance value. However, in this case, we only need moisture content (MC) accuracy to the ones place and the corresponding resistance values are so far apart that it is not vital for resistance measurements to be overly precise. A semilog plot relating the resistance and MC is found in figure 4 which illustrates this.

# Signoff Request - 4/18 - Resistance Measurement

Sunday, April 17, 2022 9:48 PM

Signoffs Page 1

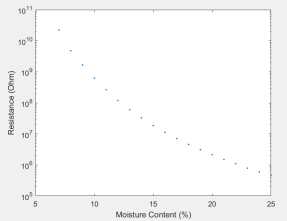
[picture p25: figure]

Figure 5: Resistance vs. MC

The circuit which will perform the measurements, as well as auto-ranging, is found in figure 6. Manual 5V and 0V nodes were used to simulate the control that the Arduino would perform. The specific mosfets were chosen because they are common, easily available PNPs with a base voltage of5V. This voltage is consistent with the Arduino output and using a PNP allows for active low control. Each resistor is labeled with the minimum value it will be intended to help measure. Using this minimum value along with the next level up minimum, a middle resistance was calculated to use as R1 and then modified slightly to match standard manufactured resistance values.

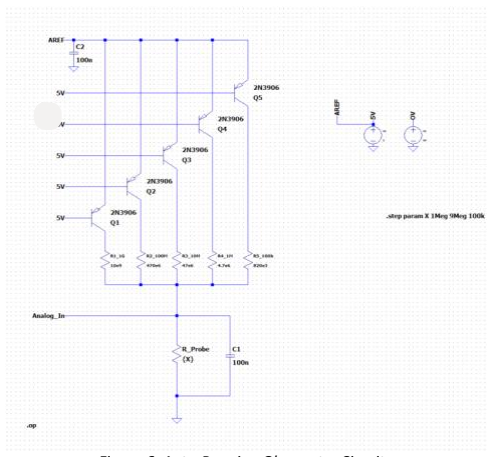
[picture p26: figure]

Figure 6: Auto-Ranging Ohmmeter Circuit Arduino ADC returns a range of 0-1023 which corresponds to a resolution of 4.88mV. This means that if values are less than 4.88mV apart the Arduino will not be able to differentiate them. Figure 7 shows the voltage values that will be read by the Arduino for each 1% moisture content. Also included in the far right column is the difference between each moisture content's corresponding voltage. The different colors represent which resistor in the voltage divider will be set active. This will be set by the program which will test starting at the highest range and lower until it is getting values withing a .5-4 volt range. The edge cases are highlighted to show they will be tested in two ranges of the ohmmeter circuit in order to ensure there is no error. Looking at the right column of the table shows that all differences are well above the resolution of 0.00488 V which means the Arduino will be able to differentiate each 1% MC value from the next MC value. The value which the Arduino will read is also included

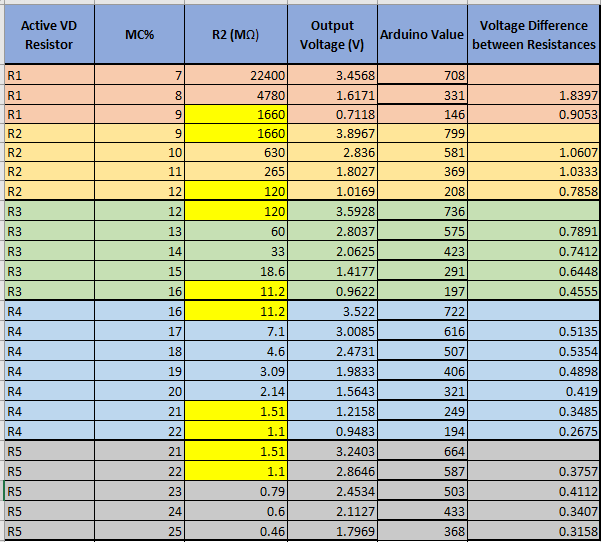
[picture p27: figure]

Figure 7: Voltage Resolution

A proximity sensor is also being included to tell the arm when to stop raising. The B5W-LA01 sensor was chosen for its range of 22.8 to 70 mm or 0.90 to 2.75 inches.

Because the linear actuator chosen in the mechanical signoff has a stroke of 100 mm this is right in the desired range for the stop signal. The proximity sensor will work better than a distance sensor because it will simply give an on when it hits its range which means an analog voltage value won't have to be read or filtered. The final schematic including this part and the motors picked in the mechanical section is found in figure 8.

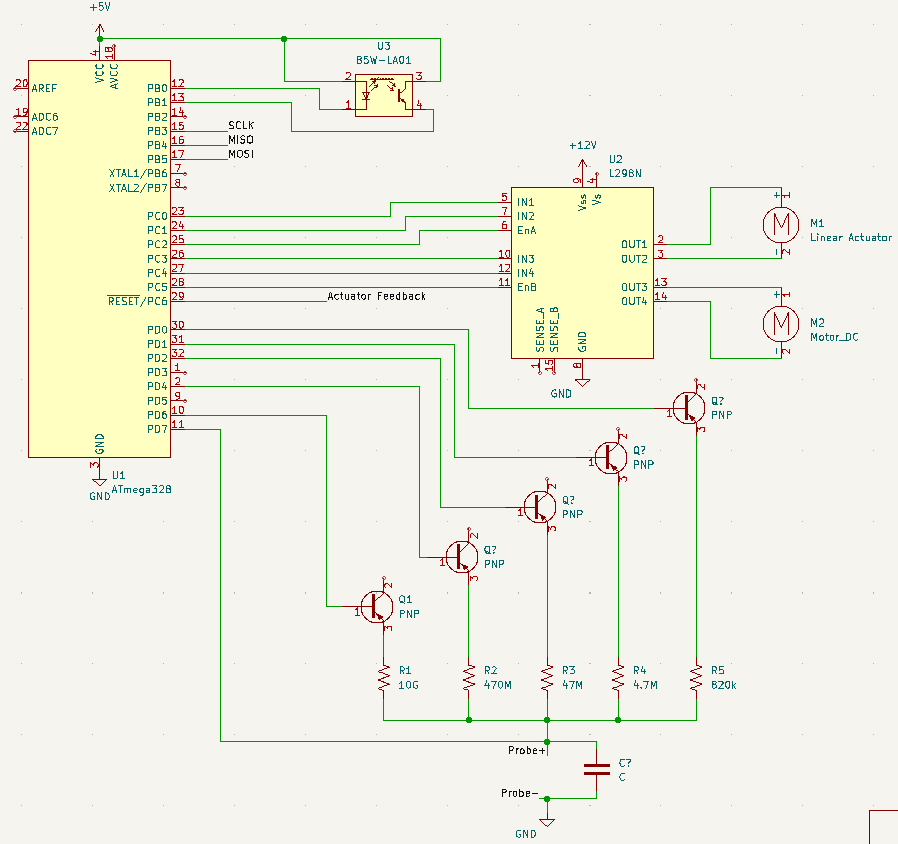
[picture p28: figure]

Figure 8: Final Schematic

Finally, in the table below a list of part numbers is included for this signoff. It is likely a PCB will be necessary for this circuit but that will be designed once the circuit design has been approved.

Part Number | Price | QTY | Description | Value | Supplier
2N3906 | $0.05 | 5 | MOSFET | PNP | Mouser (https://www.mouser.com/ProductDetail/Diotec-Semiconductor/2N3906?qs=OlC7AqGiEDn9iNua9L%252BEvw%3D%3D)
C1206F104K5RACAUTO | $0.49 | 2 | Capacitor | 100nF | Mouser (https://www.mouser.com/ProductDetail/KEMET/C1206F104K5RACAUTO?qs=sSYV1F9c5cHirYoKQC3eNA%3D%3D)
RH73X2B10GKTN | $4.57 | 1 | Resistor | 10G | Mouser (https://www.mouser.com/ProductDetail/TE-Connectivity-Holsworthy/RH73X2B10GKTN?qs=ip69W3eHERXIsO3Uinul1A%3D%3D)
CRCW1206470MJPEAHR | $0.69 | 1 | Resistor | 470M | Mouser (https://www.mouser.com/ProductDetail/Vishay-Dale/CRCW1206470MJPEAHR?qs=0LP1uVfdam%252BJni%252BOw51DXQ%3D%3D)
CRCW120647M0JPEAHR | $0.69 | 1 | Resistor | 47M | Mouser (https://www.mouser.com/ProductDetail/Vishay-Dale/CRCW120647M0JPEAHR?qs=TwJWXEwNN6Th6A2%252BYjAylw%3D%3D)
CR1206-FW-4704ELF | $0.10 | 1 | Resistor | 4.7M | Mouser (https://www.mouser.com/ProductDetail/Bourns/CR1206-FW-4704ELF?qs=6oMev5NRZMESIfn0oPpnuQ%3D%3D)
CR1206-FX-8203ELF | $0.10 | 1 | Resistor | 820k | Mouser (https://www.mouser.com/ProductDetail/Bourns/CR1206-FX-8203ELF?qs=x5wsLs3ZZ823UExx6LZy8Q%3D%3D)
B5W-LA01 | 7.45 | 1 | Proximity Sensor | 22.8mm - 70mm | Mouser (https://www.mouser.com/ProductDetail/Omron-Electronics/B5W-LA01?qs=k%252B6EXM6KU1Mnfx0L%2FHew1Q%3D%3D)
L298N | 6.99 | 1 | Motor Driver | | Amazon (https://www.amazon.com/Qunqi-Controller-Module-Stepper-Arduino/dp/B014KMHSW6?hvadid=167139094796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)
[1] William L. James. Electric Moisture Meters for Wood. USDA. https://www.fpl.fs.fed.us/documnts/fplgtr/fplgtr06.pdf. (Accessed April 16, 2022).
[2] Matthias Swandel. Wood Mositure Meter. WoodGear.Ca. https://woodgears.ca/lumber/moisture_meter.html. (Accessed April 16, 2022).
[3] Multimeter Click. Mikroe. https://www.mikroe.com/multimeter-click. (Accessed April 16, 2022)
[4] Arduino Based Auto-Ranging Ohmeter. Simple Projects. https://simple-circuit.com/arduino-auto-ranging-ohmmeter-lcd/(Accessed April 27, 2022).

12

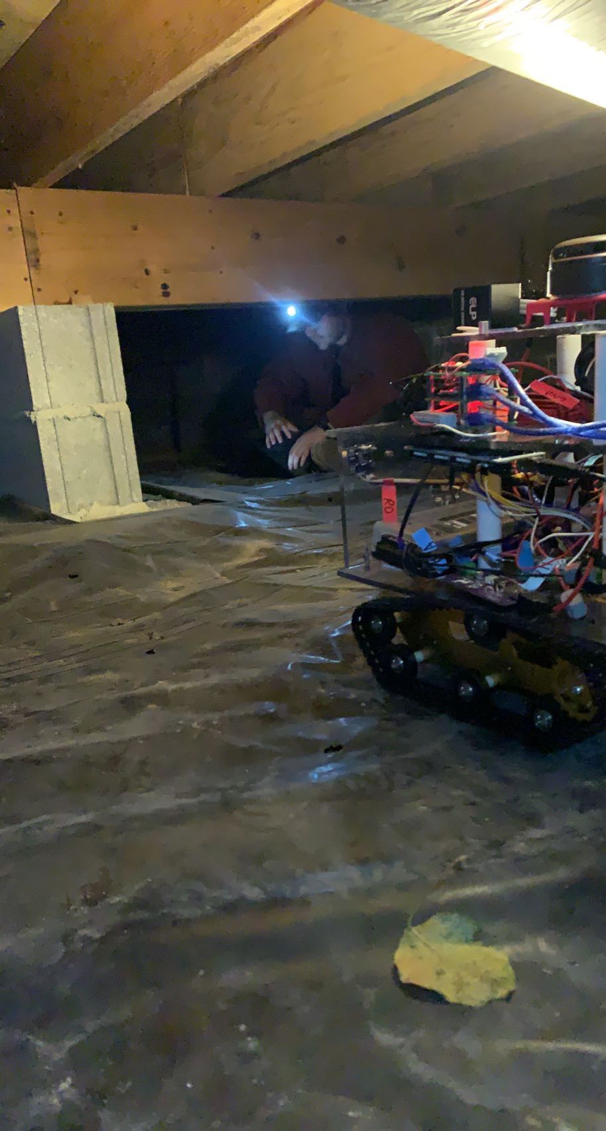
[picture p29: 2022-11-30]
Pictures and Videos/Crawlspace_Test.jpg

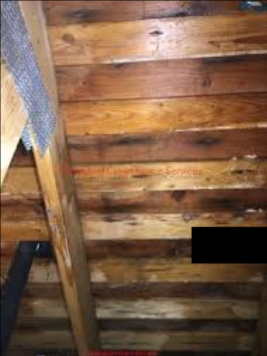
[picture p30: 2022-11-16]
Pictures and Videos/Experiment_Pictures/Crawlspace1_Result.png

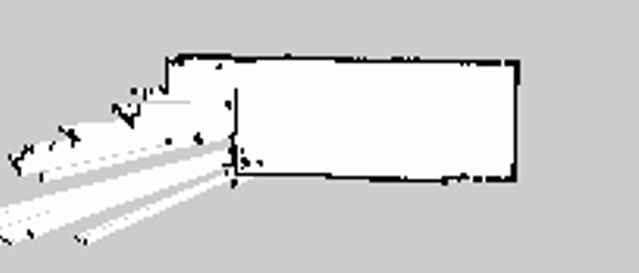
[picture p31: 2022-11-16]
Pictures and Videos/Experiment_Pictures/ROSGeneratedMaps/ROS_Crawlspace_Map_V2.PNG

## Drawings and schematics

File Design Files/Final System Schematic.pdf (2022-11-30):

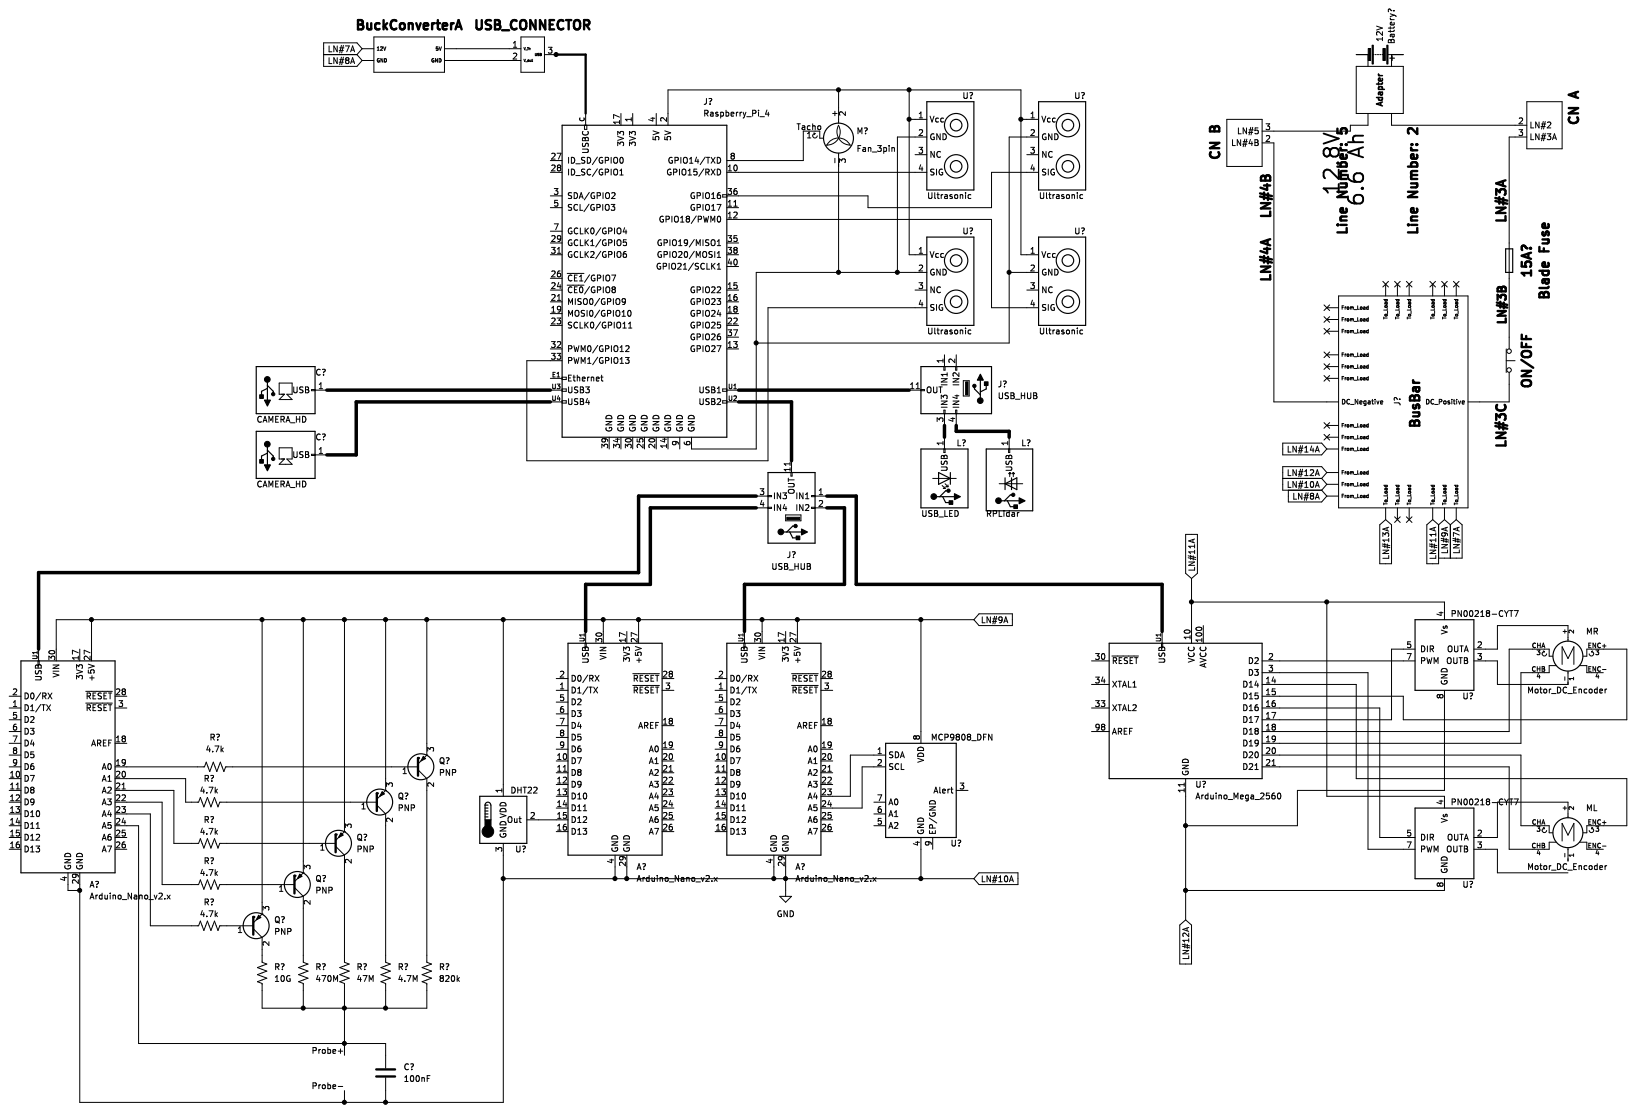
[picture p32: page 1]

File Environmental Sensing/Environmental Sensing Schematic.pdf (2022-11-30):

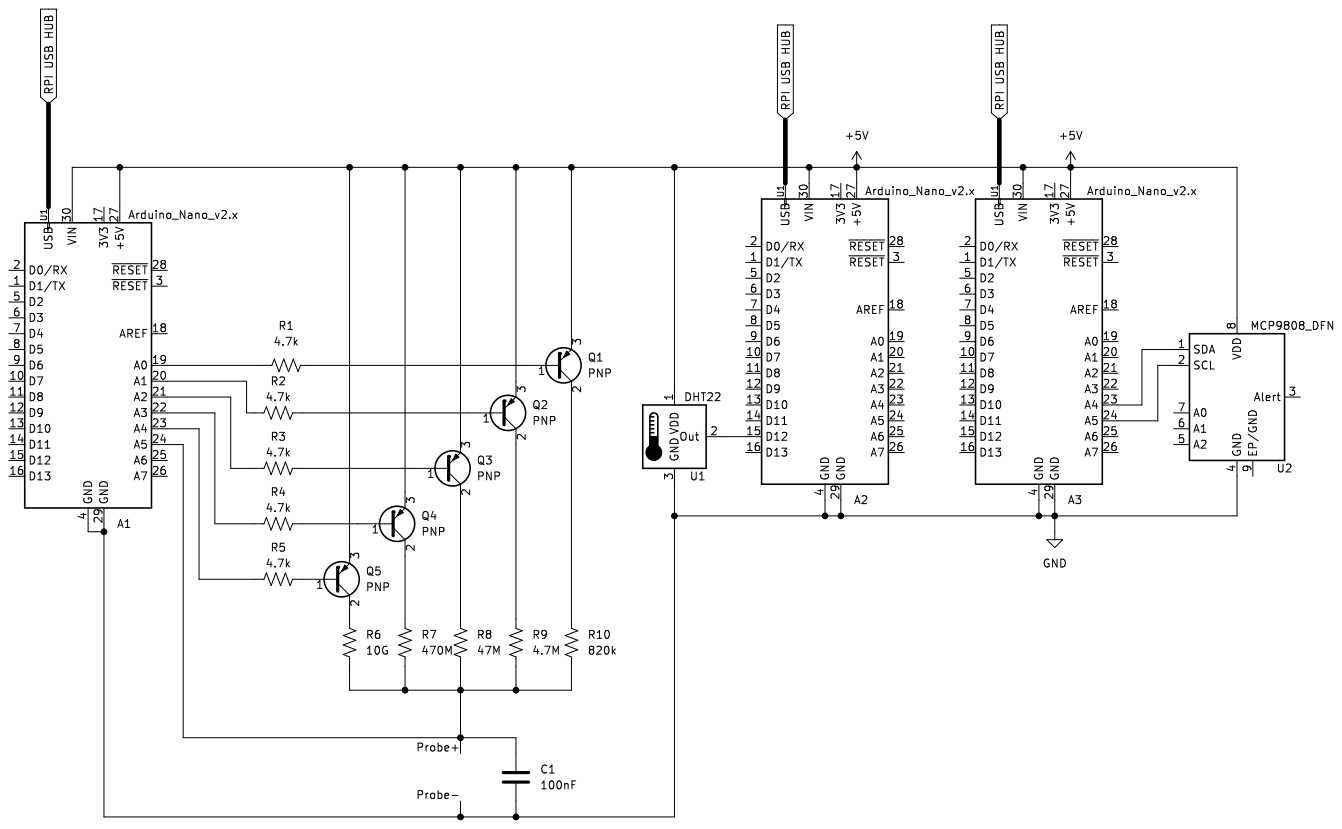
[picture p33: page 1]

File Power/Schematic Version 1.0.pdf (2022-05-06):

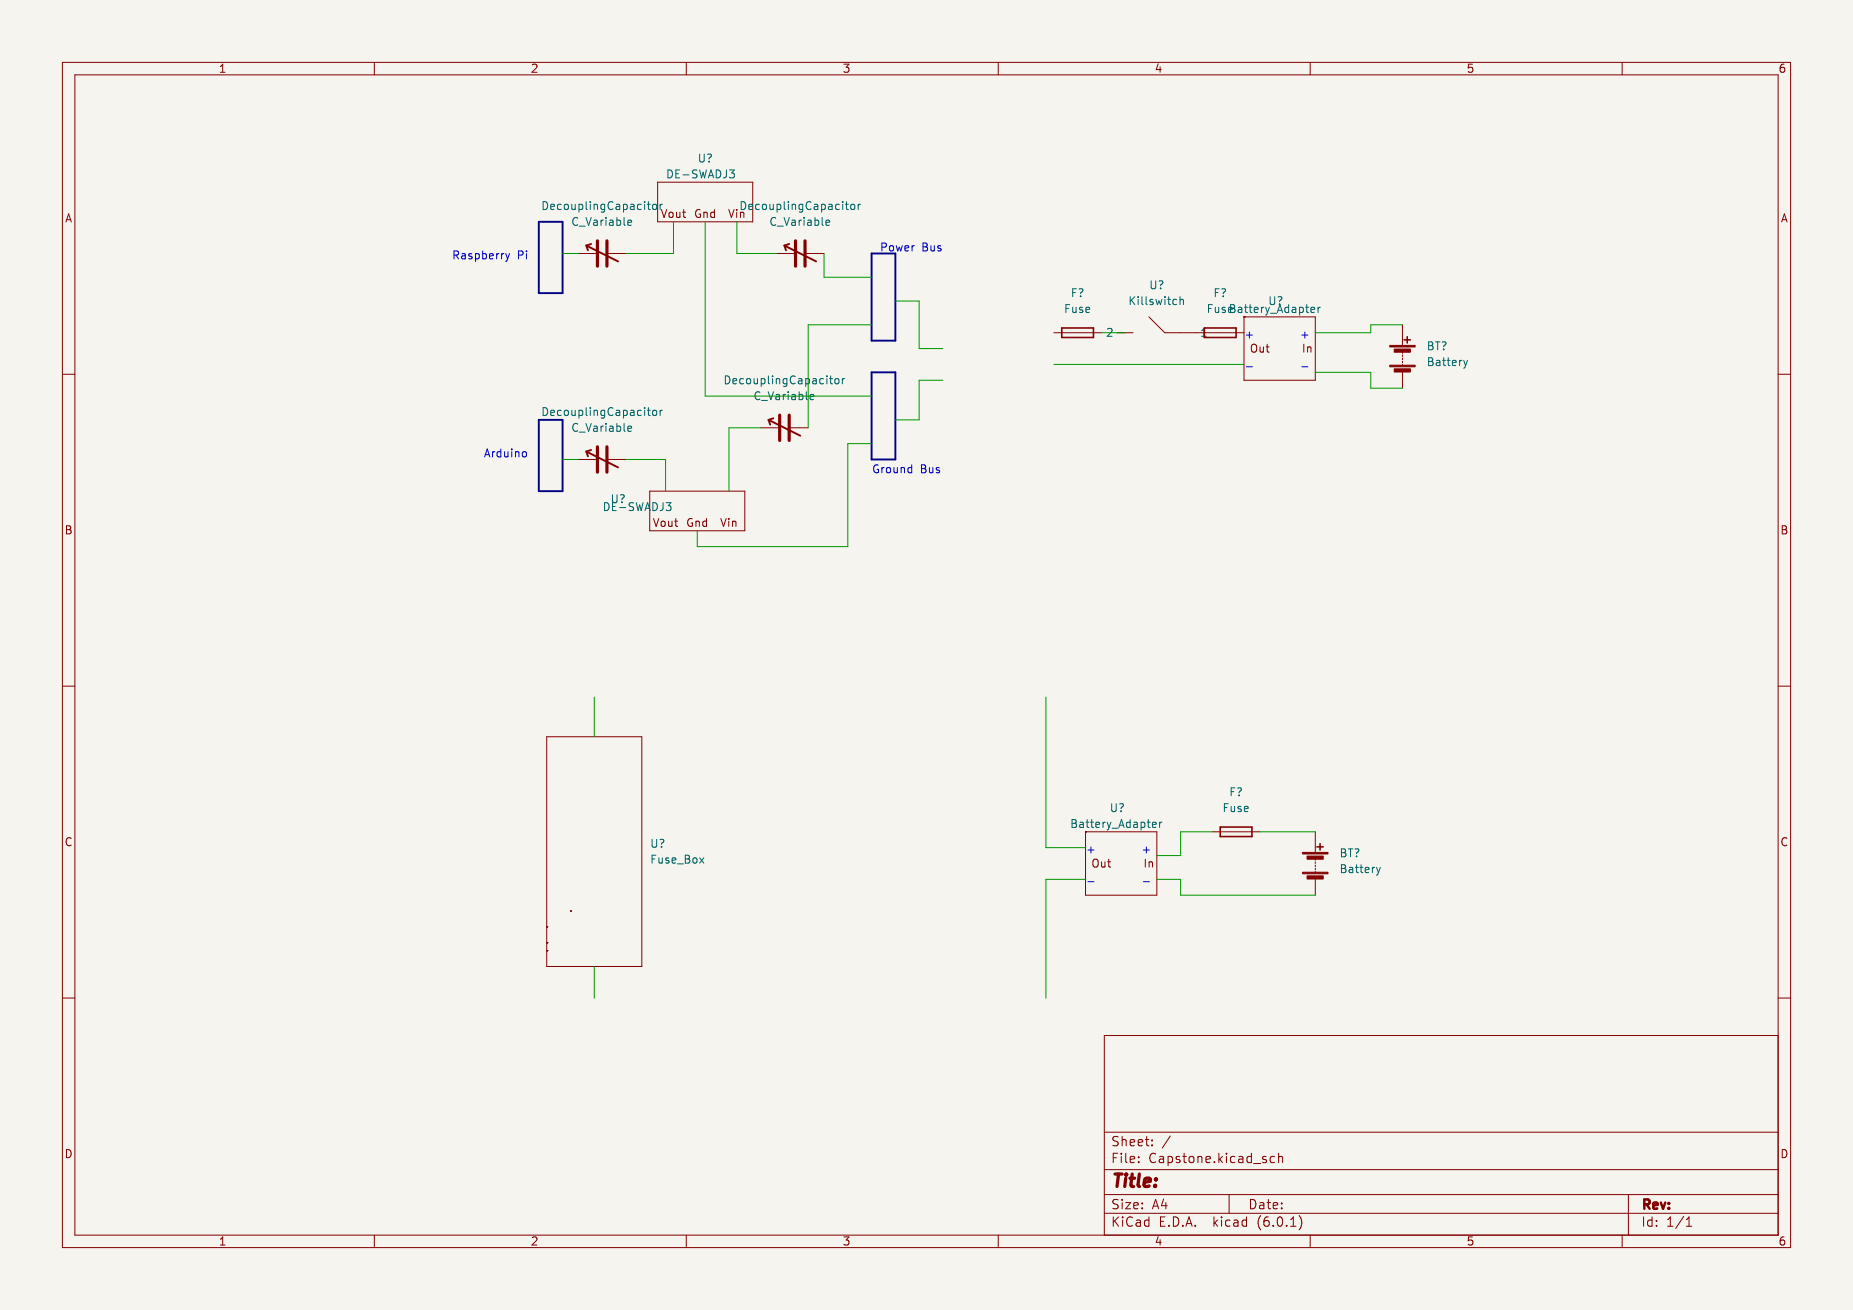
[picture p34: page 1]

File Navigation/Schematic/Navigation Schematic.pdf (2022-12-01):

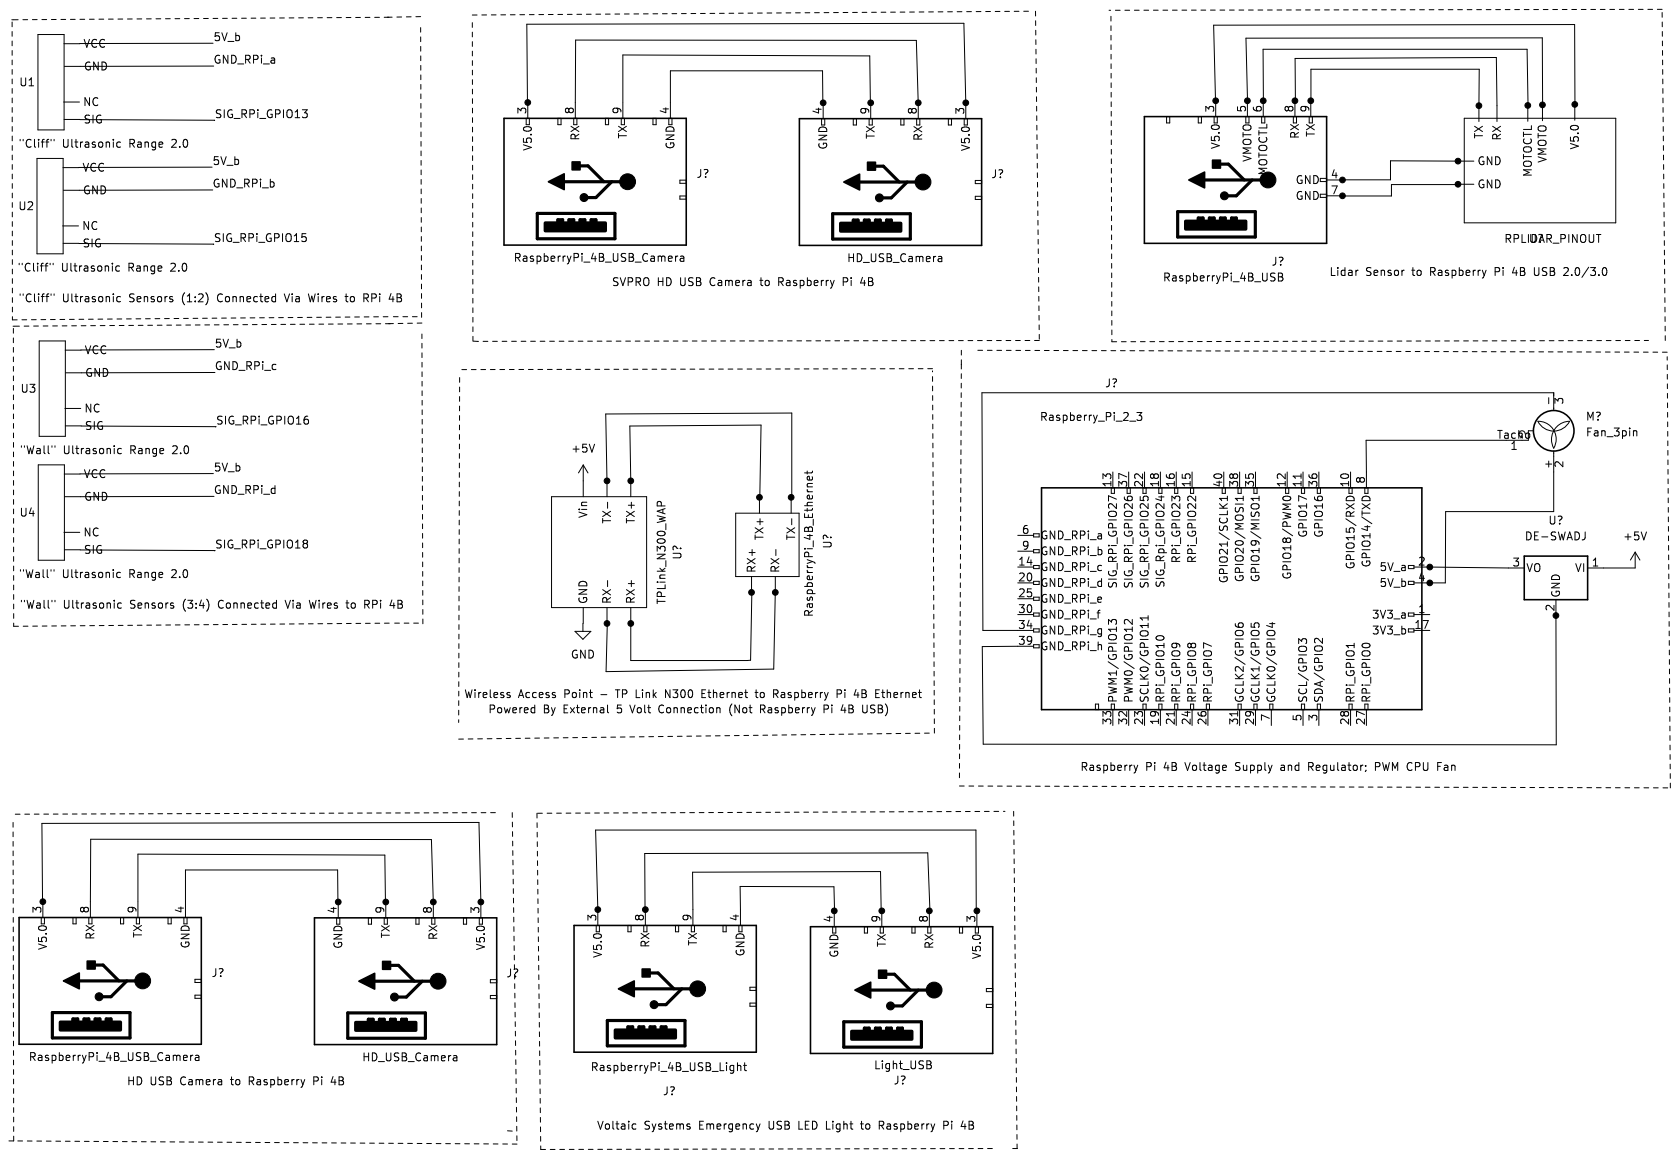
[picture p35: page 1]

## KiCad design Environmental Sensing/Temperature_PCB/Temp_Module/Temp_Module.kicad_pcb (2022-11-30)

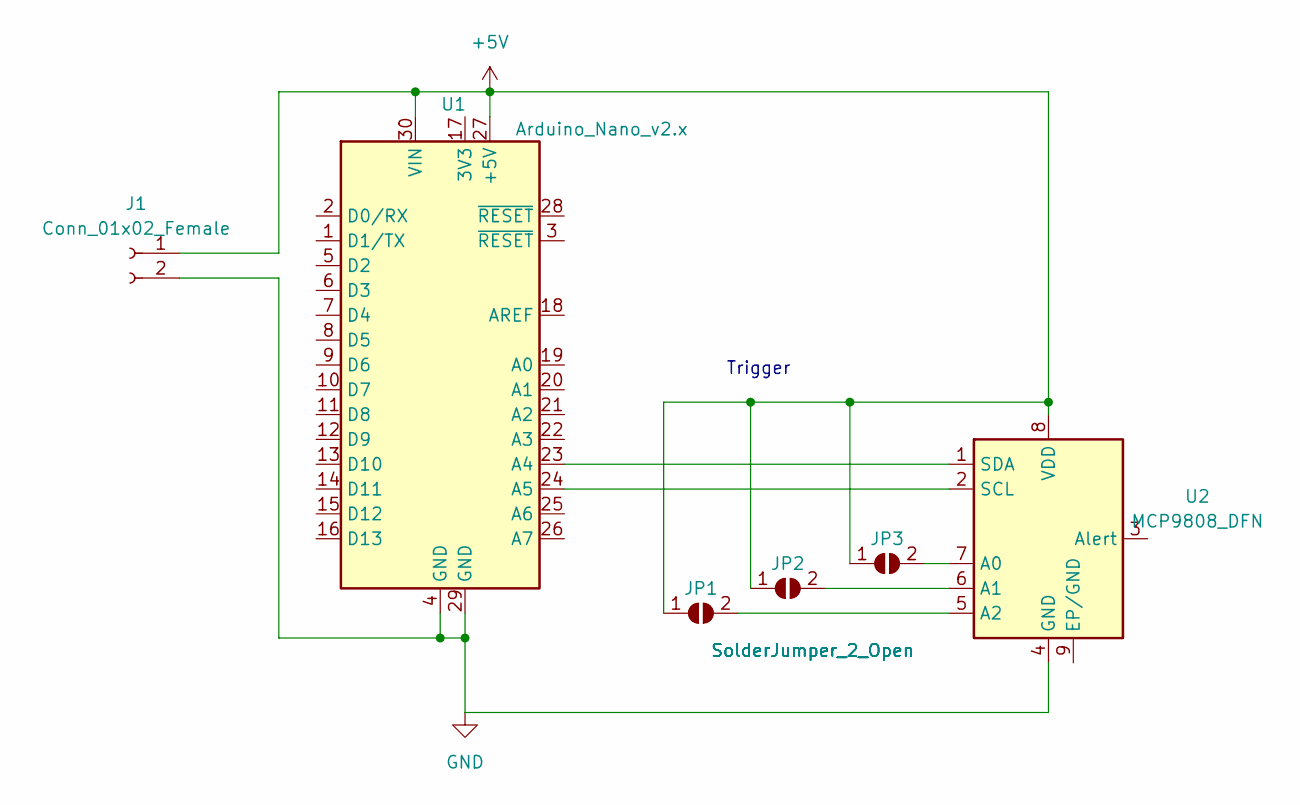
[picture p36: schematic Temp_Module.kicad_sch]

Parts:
J1: Conn_01x02_Female; PinHeader_1x02_P2.54mm_Vertical
JP1, JP2, JP3: SolderJumper_2_Open; SolderJumper-2_P1.3mm_Bridged2Bar_Pad1.0x1.5mm
U1: Arduino_Nano_v2.x; Arduino_Nano_WithMountingHoles
U2: MCP9808_DFN; DFN-8-1EP_3x2mm_P0.5mm_EP1.7x1.4mm

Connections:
+5V: J1.1, JP1.1 (A), JP2.1 (A), JP3.1 (A), U1.27 (+5V), U1.30 (VIN), U2.8 (VDD)
GND: J1.2, U1.4 (GND), U1.29 (GND), U2.4 (GND)
unnamed: JP1.2 (B), U2.5 (A2)
unnamed: JP2.2 (B), U2.6 (A1)
unnamed: JP3.2 (B), U2.7 (A0)
unnamed: U1.23 (A4), U2.1 (SDA)
unnamed: U1.24 (A5), U2.2 (SCL)

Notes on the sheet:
Trigger

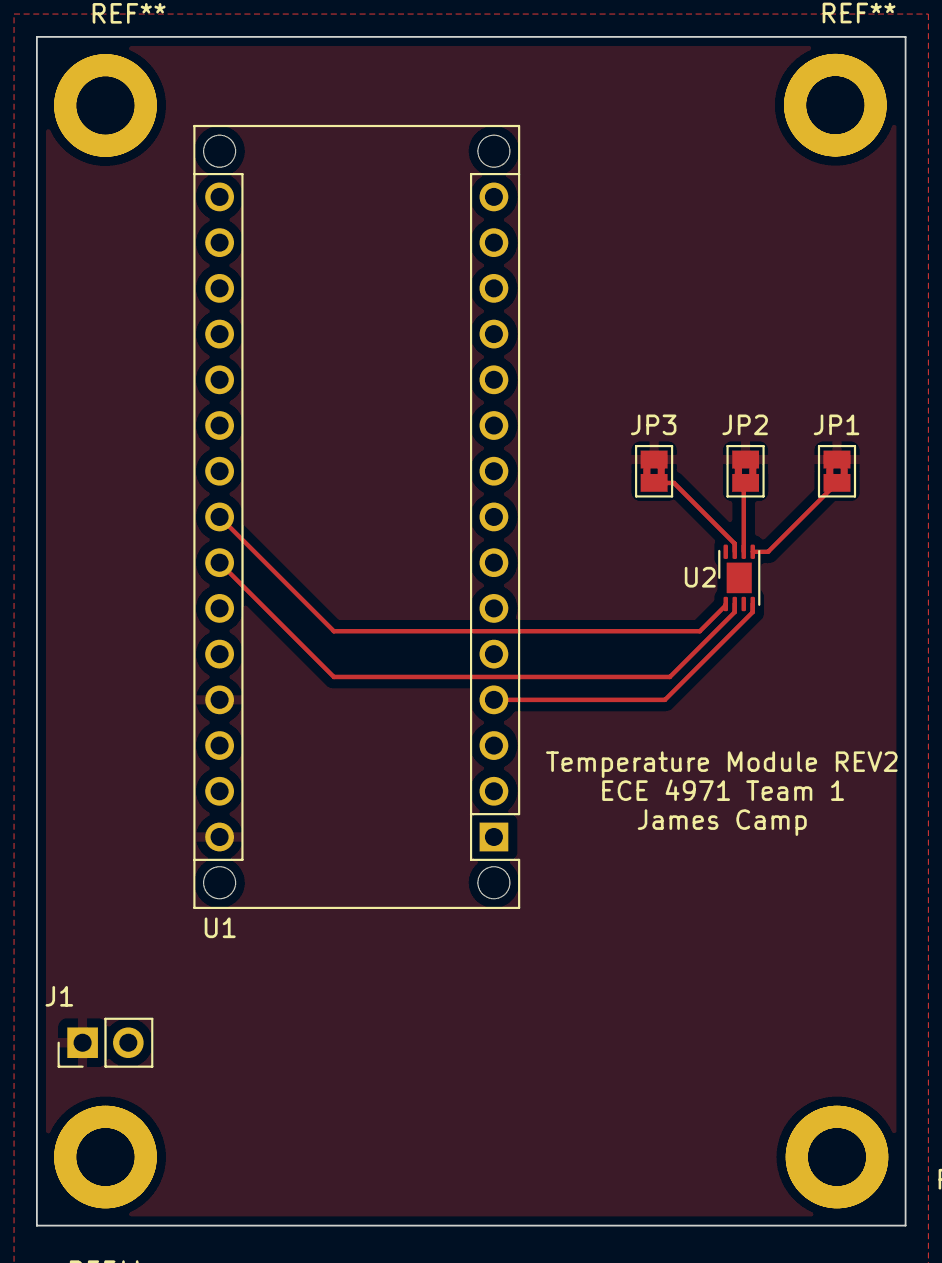
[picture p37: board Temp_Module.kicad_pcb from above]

Board: 2 copper layers, 48.3 x 66.0 mm, 6 parts (0 on the bottom side), 7 nets.

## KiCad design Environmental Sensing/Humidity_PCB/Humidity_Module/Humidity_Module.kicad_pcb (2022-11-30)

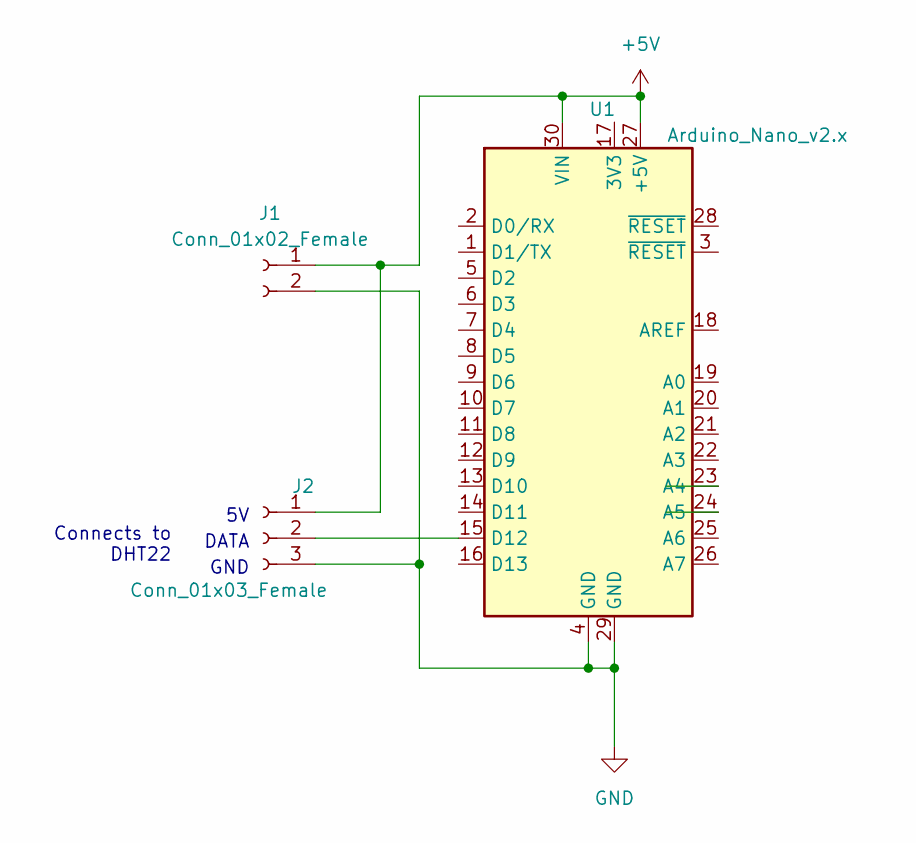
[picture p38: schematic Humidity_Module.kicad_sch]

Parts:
J1: Conn_01x02_Female; PinHeader_1x02_P2.54mm_Vertical
J2: Conn_01x03_Female; PinHeader_1x03_P2.54mm_Horizontal
U1: Arduino_Nano_v2.x; Arduino_Nano

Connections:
+5V: J1.1, J2.1, U1.27 (+5V), U1.30 (VIN)
GND: J1.2, J2.3, U1.4 (GND), U1.29 (GND)
unnamed: J2.2, U1.15 (D12)

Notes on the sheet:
Connects to DHT22
GND
DATA

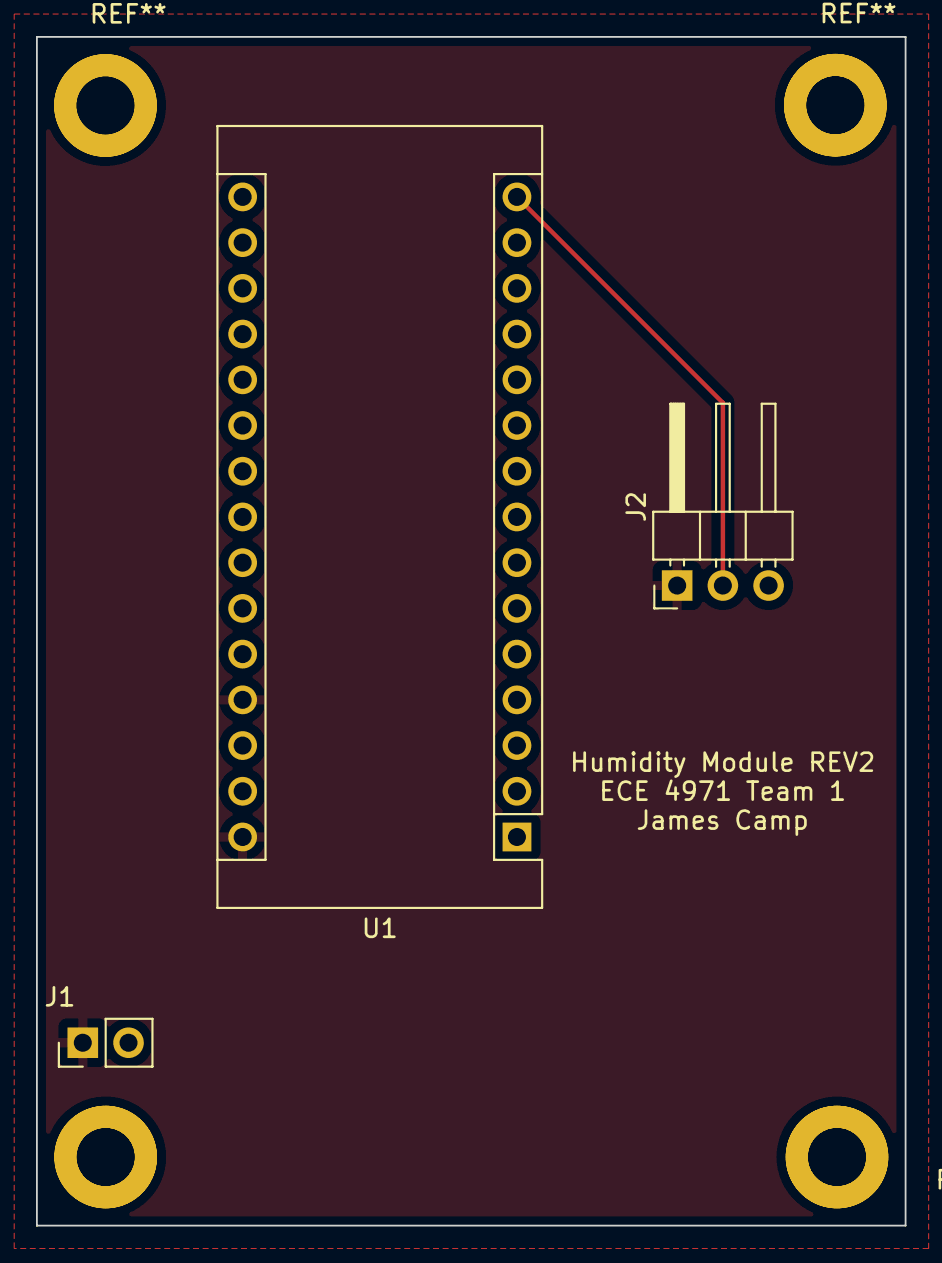
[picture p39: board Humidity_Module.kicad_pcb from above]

Board: 2 copper layers, 48.3 x 66.0 mm, 3 parts (0 on the bottom side), 3 nets.

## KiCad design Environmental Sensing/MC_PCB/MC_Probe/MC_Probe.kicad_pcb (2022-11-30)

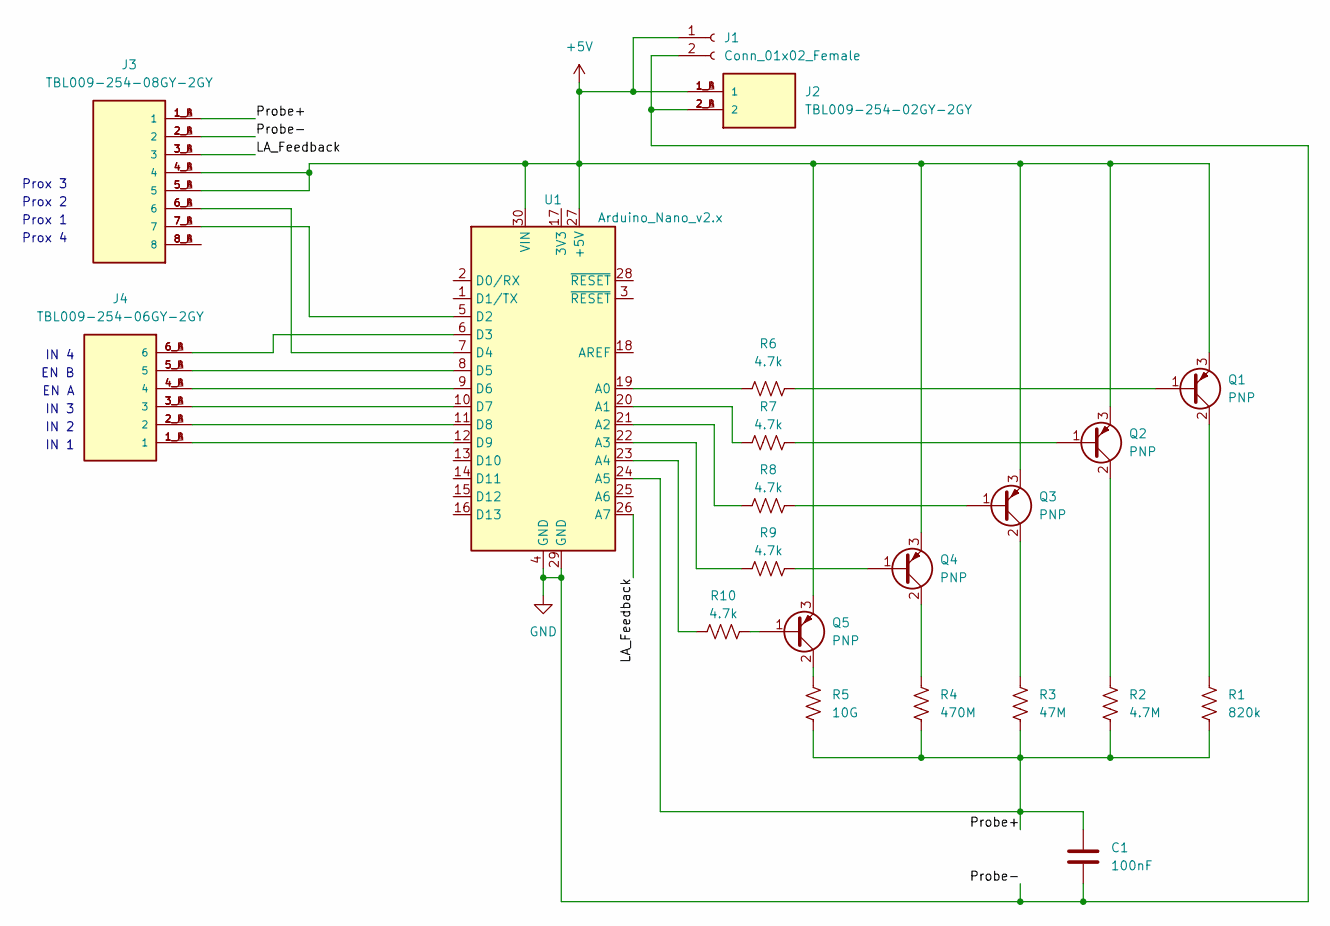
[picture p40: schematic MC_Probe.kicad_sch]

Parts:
C1: 100nF; C_1206_3216Metric
J1: Conn_01x02_Female; PinHeader_1x02_P2.54mm_Vertical
J2: TBL009-254-02GY-2GY; CUI_TBL009-254-02GY-2GY
J3: TBL009-254-08GY-2GY; CUI_TBL009-254-08GY-2GY
J4: TBL009-254-06GY-2GY; CUI_TBL009-254-06GY-2GY
Q1, Q2, Q3, Q4, Q5: PNP; TO-92
R1: 820k; R_1206_3216Metric
R2: 4.7M; R_1206_3216Metric
R3: 47M; R_1206_3216Metric
R4: 470M; R_1206_3216Metric
R5: 10G; R_1206_3216Metric
R6, R7, R8, R9, R10: 4.7k; R_1206_3216Metric
U1: Arduino_Nano_v2.x; Arduino_Nano_WithMountingHoles

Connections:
+5V: J1.1, J2.1_A (1), J2.1_B (1), J3.4_A (4), J3.4_B (4), J3.5_A (5), J3.5_B (5), Q1.3 (E), Q2.3 (E), Q3.3 (E), Q4.3 (E), Q5.3 (E), U1.27 (+5V), U1.30 (VIN)
/LA_Feedback: J3.3_A (3), J3.3_B (3), U1.26 (A7)
/Probe+: C1.1, J3.1_A (1), J3.1_B (1), R1.2, R2.2, R3.2, R4.2, R5.2, U1.24 (A5)
GND: C1.2, J1.2, J2.2_A (2), J2.2_B (2), J3.2_A (2), J3.2_B (2), U1.4 (GND), U1.29 (GND)
unnamed: J3.8_A (8), J3.8_B (8)
unnamed: J4.1_A (1), J4.1_B (1), U1.12 (D9)
unnamed: J4.2_A (2), J4.2_B (2), U1.11 (D8)
unnamed: J4.3_A (3), J4.3_B (3), U1.10 (D7)
unnamed: J4.4_A (4), J4.4_B (4), U1.9 (D6)
unnamed: J4.5_A (5), J4.5_B (5), U1.8 (D5)
unnamed: J4.6_A (6), J4.6_B (6), U1.6 (D3)
unnamed: Q1.1 (B), R6.2
unnamed: Q1.2 (C), R1.1
unnamed: Q2.1 (B), R7.2
unnamed: Q2.2 (C), R2.1
unnamed: Q3.1 (B), R8.2
unnamed: Q3.2 (C), R3.1
unnamed: Q4.2 (C), R4.1
unnamed: Q5.1 (B), R10.2
unnamed: Q5.2 (C), R5.1
unnamed: Q4.1 (B), R9.2
unnamed: J3.7_A (7), J3.7_B (7), U1.5 (D2)
unnamed: J3.6_A (6), J3.6_B (6), U1.7 (D4)
unnamed: R6.1, U1.19 (A0)
unnamed: R7.1, U1.20 (A1)
unnamed: R8.1, U1.21 (A2)
unnamed: R9.1, U1.22 (A3)
unnamed: R10.1, U1.23 (A4)

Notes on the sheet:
Prox 2
EN A
IN 1
EN B
IN 2
Prox 4
IN 4
Prox 3
IN 3
Prox 1

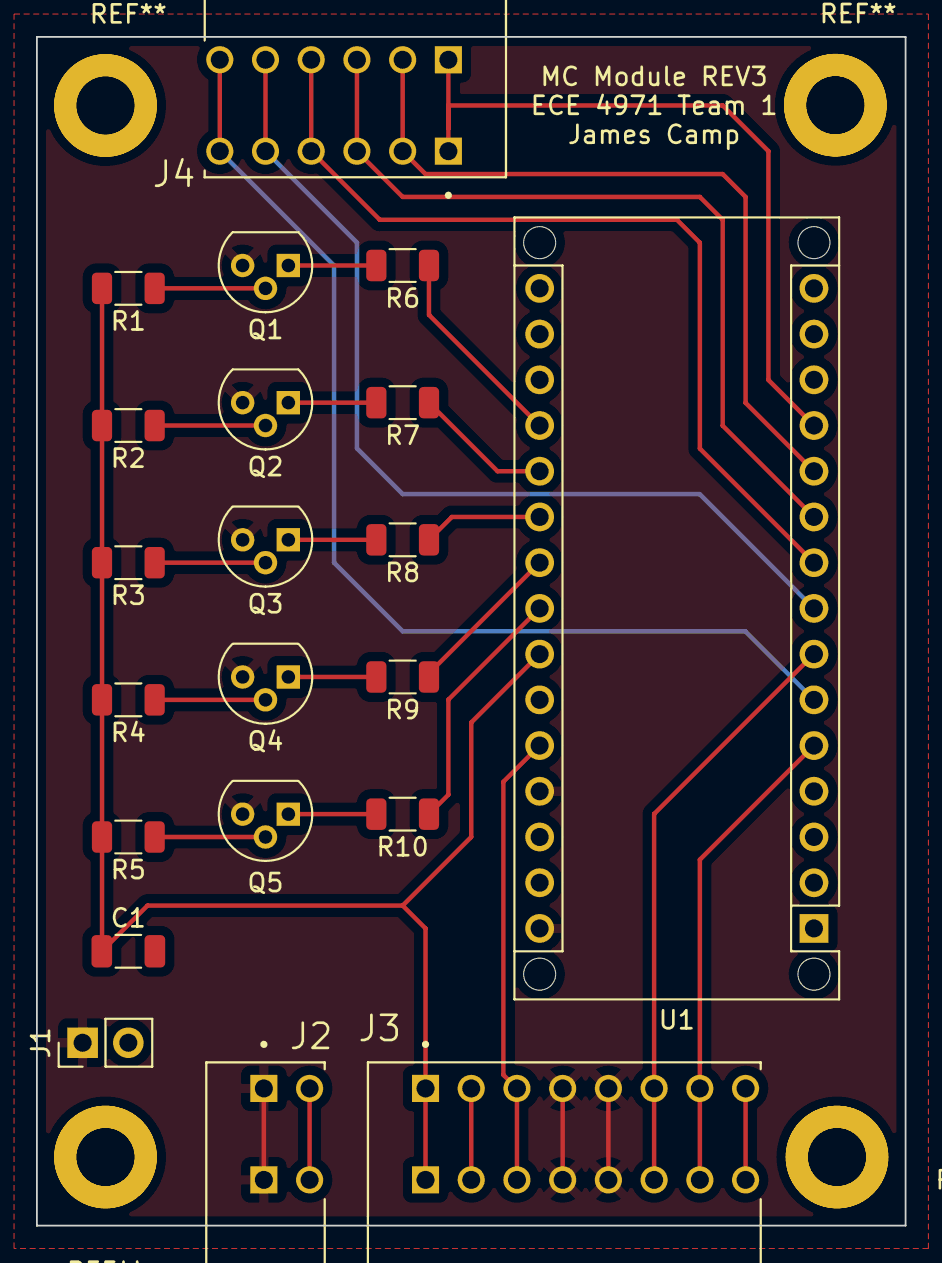
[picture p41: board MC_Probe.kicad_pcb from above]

Board: 2 copper layers, 48.3 x 66.0 mm, 21 parts (0 on the bottom side), 28 nets.

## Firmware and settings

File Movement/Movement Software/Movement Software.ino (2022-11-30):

const int M1channel1 = 18; //here we assign the encoder channels to their pin numbers
const int M1channel2 = 19;
const int M2channel1 = 20;
const int M2channel2 = 21;
const int M1PWM = 2; // the outputs to the drivers are linked to pin numbers
const int M1DIR = 17;
const int M2PWM = 3;
const int M2DIR = 16;
const int Encoder1Power = 15; //These pins power the encoders
const int Encoder2Power = 14;
char direct = 'S'; // This is the serial input from Raspberry Pi
volatile float M1C1freq = 0; //initalize the frequency from encoders
volatile float M1C2freq = 0;
volatile float M2C1freq = 0;
volatile float M2C2freq = 0;
float M1C1rpm;
float M1C2rpm;
float M2C1rpm;
float M2C2rpm;

void setup() {

 //setup the inputs to receive encoder data
pinMode(M1channel1, INPUT); 
pinMode(M1channel2, INPUT);
pinMode(M2channel1, INPUT);
pinMode(M2channel2, INPUT);

 //setup the outputs to the motor drivers
pinMode(M1PWM, OUTPUT);
pinMode(M1DIR, OUTPUT);
pinMode(M2PWM, OUTPUT);
pinMode(M2DIR, OUTPUT);

// Output Power to the Encoders
pinMode(Encoder1Power, OUTPUT);
pinMode(Encoder2Power, OUTPUT);
digitalWrite(Encoder1Power, HIGH);
digitalWrite(Encoder2Power, HIGH);

//setup the interrupts to detect the CPR of the motor encoders
//attachInterrupt(digitalPinToInterrupt(18), readM1Channel1, CHANGE);
//attachInterrupt(digitalPinToInterrupt(19), readM1Channel2, CHANGE);
//attachInterrupt(digitalPinToInterrupt(20), readM2Channel1, HIGH);
//attachInterrupt(digitalPinToInterrupt(21), readM2Channel2, CHANGE); 

//Open Serial Monitor
Serial.begin(9600);
}

void loop() { 

// That char variable is used to determine the direction of movement. 
if(Serial.available()){
        direct = Serial.read();
        delay(250);
}
// The next four If statements use the direct char from raspberry pi
// and change the direction of the motors accordingly
if (direct == 'F'){ //FORWARD
  digitalWrite(M1DIR, HIGH);
  digitalWrite(M2DIR, HIGH);
  analogWrite(M1PWM, 175);
  analogWrite(M2PWM, 175);
}
delay(20);
if (direct =='B'){ //BACKWARD
  digitalWrite(M1DIR, LOW);
  digitalWrite(M2DIR, LOW);
  analogWrite(M1PWM, 175);
  analogWrite(M2PWM, 175);
}
delay(20);
if (direct =='L'){ //LEFT
  digitalWrite(M1DIR, HIGH);
  digitalWrite(M2DIR, LOW);
  analogWrite(M1PWM, 100);  
  analogWrite(M2PWM, 100);
}
delay(20);
if (direct =='R'){ //RIGHT
  digitalWrite(M1DIR, LOW);
  digitalWrite(M2DIR, HIGH);
  analogWrite(M1PWM, 100);
  analogWrite(M2PWM, 100);
}

delay(20);
if (direct =='S'){ //STOP  
  analogWrite(M1PWM, 0);
  analogWrite(M2PWM, 0);
}

// Convert Pulse Frequencies to Speeds
M1C1rpm = M1C1freq * 1.27 / 12;
//float M1C2rpm = M1C2freq / 12;
M2C1rpm = M2C1freq * 1.27  / 12;
//float M2C2rpm = M2C2freq / 12;

//Output Speeds to Pi
delay(250);
Serial.println(M1C1rpm);
//Serial.println(M1C2rpm);
Serial.println(M2C1rpm);
//Serial.println(M2C2rpm);

attachInterrupt(digitalPinToInterrupt(18), readM1Channel1, HIGH);
//attachInterrupt(digitalPinToInterrupt(19), readM1Channel2, HIGH);
attachInterrupt(digitalPinToInterrupt(20), readM2Channel1, HIGH);
//attachInterrupt(digitalPinToInterrupt(21), readM2Channel2, HIGH);
}

//Now I need to read the Encoder channels with those ISRs
//I'm also calculating the frequency of the pulses in here
void readM1Channel1(){
if(direct != 'S'){
  float M1C1high = pulseIn(M1channel1,HIGH);
  float M1C1low = pulseIn(M1channel1,LOW);
  M1C1freq = 1000000 / (M1C1high + M1C1low);
  detachInterrupt(digitalPinToInterrupt(18));
  }
  else 
  M1C1freq = 0;
  detachInterrupt(digitalPinToInterrupt(18));
}

/*void readM1Channel2(){
if(direct != 'S'){
  float M1C2high = pulseIn(M1channel2,HIGH);
  float M1C2low = pulseIn(M1channel2,LOW);
  M1C2freq = 1000000 / (M1C2high + M1C2low);
  detachInterrupt(digitalPinToInterrupt(19));
  }
  else 
  M1C2freq = 0;
  detachInterrupt(digitalPinToInterrupt(19));
}*/

void readM2Channel1(){
  if(direct != 'S'){
  float M2C1high = pulseIn(M2channel1,HIGH);
  float M2C1low = pulseIn(M2channel1,LOW);
  M2C1freq = 1000000 / (M2C1high + M2C1low);
  detachInterrupt(digitalPinToInterrupt(20));
  }
  else 
  M2C1freq = 0;
  detachInterrupt(digitalPinToInterrupt(20));
}

/*void readM2Channel2(){
if(direct != 'S'){
  float M2C2high = pulseIn(M2channel2,HIGH);
  float M2C2low = pulseIn(M2channel2,LOW);
  M2C2freq = 1000000 / (M2C2high + M2C2low);
  detachInterrupt(digitalPinToInterrupt(21));
  }
  else 
  M2C2freq = 0;
  detachInterrupt(digitalPinToInterrupt(21));
}*/

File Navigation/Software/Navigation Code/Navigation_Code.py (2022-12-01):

#!/usr/bin/python3
import RPi.GPIO as GPIO
import time
import serial
import string
from threading import Thread
import numpy as np
import cv2

# Open the serial port between the Raspberry Pi 4B and the Arduino

ser = serial.Serial('/dev/ttyACM0', 9600)
temp = serial.Serial('/dev/ttyUSB3', 9600)
hum = serial.Serial('/dev/ttyUSB2', 9600)
mc = serial.Serial('/dev/ttyUSB1', 9600)
time.sleep(0.2)

FRONT_GPIO = 15
LEFT_CORNER_GPIO = 13
RIGHT_CORNER_GPIO = 16

temps = []
hums = []
mcs = []

print(temps)
print(hums)
print(mcs)


def takePic(dc):
    print("In this biotch")
# creating the videocapture object
    # and reading from the input file
    # Change it to 0 if reading from webcam
    cap = cv2.VideoCapture("v4l2src ! image/jpeg, width=1280, height=720, framerate=30/1 ! jpegdec ! videoconvert ! video/x-raw, format=BGR ! appsink ")

    #cap2 = cv2.VideoCapture("v4l2src device=/dev/video2 ! image/jpeg, width=1280, height=720, framerate=30/1 ! jpegdec ! videoconvert ! video/x-raw, format=BGR ! appsink ")


    # used to record the time when we processed last frame
    prev_frame_time = 0
    #prev_frame_time2 = 0 
    # used to record the time at which we processed current frame
    new_frame_time = 0
    #new_frame_time2 = 0
    # Declaring Base Path Name for Wall and Ceiling Frames
    #wall_frame_base_path = ("/home/ubuntu/Desktop/ECE_4961_4971_Autonomous_Crawlspace_Inspection_Robot/Crawlspace_Images")
    #wall_frame_base_name = ("wall_frame")
    ceiling_frame_base_path = ("/home/ubuntu/Desktop/ECE_4961_4971_Autonomous_Crawlspace_Inspection_Robot/Crawlspace_Images")
    ceiling_frame_base_name = ("ceiling_frame")

    # Reading the video file until finished
    while(cap.isOpened()): #& cap2.isOpened()):
 
        # Capture frame-by-frame
        ret, frame = cap.read()
        #ret2, frame2 = cap2.read()
 
        # if video finished or no Video Input
        if not ret: # & ret2:
            break
 
        # Our operations on the frame come here
        gray = frame
        #gray2 = frame2
        # resizing the frame size according to our need
        gray = cv2.resize(gray, (1280,720))
        #gray2 = cv2.resize(gray2, (1280,720))
 
        # font which we will be using to display FPS
        font = cv2.FONT_HERSHEY_SIMPLEX
        #font2 = cv2.FONT_HERSHEY_SIMPLEX
        # time when we finish processing for this frame
        new_frame_time = time.time()
        #new_frame_time2 = time.time()
        # Calculating the fps
 
        # fps will be number of frame processed in given time frame
        # since their will be most of time error of 0.001 second
        # we will be subtracting it to get more accurate result
        fps = 1/(new_frame_time-prev_frame_time)
        prev_frame_time = new_frame_time
     
        #fps2 = 1/(new_frame_time2-prev_frame_time2)
        #prev_frame_time2 = new_frame_time2
 
 
        # converting the fps into integer
        fps = int(fps)
        #fps2 = int(fps2)
        # converting the fps to string so that we can display it on frame
        # by using putText function
        fps = str(fps)
        #fps2 = str(fps2)
        # putting the FPS count on the frame
        cv2.putText(gray, fps, (7, 70), font, 3, (100, 255, 0), 3, cv2.LINE_AA)
        #cv2.putText(gray2, fps2, (7, 70), font2, 3, (100, 255, 0), 3, cv2.LINE_AA)
        # displaying the frame with fps
        cv2.imshow('frame', gray)
        #cv2.imshow('frame2', gray2)
        # function for capturing/saving image

        #if cv2.waitKey(1) & 0xFF == ord('c'):
            #break
        print("About to If")
        if cv2.waitKey(1):
            ceiling_outfile = '%s/%s.jpg' % (ceiling_frame_base_path, str(dc))
            #wall_outfile = '%s/%s.jpg' % (wall_frame_base_path, wall_frame_base_name + str(dc))
            time.sleep(3)
            print("Slept")
            cv2.imwrite(ceiling_outfile, frame)
            #v2.imwrite(wall_outfile, frame2)
        print("About To If 2")
        # press 'Q' if you want to exit
        if cv2.waitKey(1): #& 0xFF == ord('q'):
            break
 
    # When everything done, release the capture
    cap.release()
    # Destroy the all windows now
    cv2.destroyAllWindows()
    print("About To Return")

# Function To Get and Print Data - Will Execute 100 Times Then Clearn Up
def getandPrint():

    print("SeeedStudio Grove Ultrasonic Get Data and Print")

    # test 100 times
    for i in range(100):
        measurementInCM()

    # Reset GPIO Settings
    # Clean Ups All Pins I Have Set In This .Py
    GPIO.cleanup()

# Function To Get Measurements From GPIO Pins (Start and Stop)
def measurementInCM(): 

    # Setup GPIO_SIGs As Outputs
    GPIO.setup(FRONT_GPIO, GPIO.OUT)
    GPIO.setup(LEFT_CORNER_GPIO,GPIO.OUT)
    GPIO.setup(RIGHT_CORNER_GPIO,GPIO.OUT)

    # Output Low on GPIO_SIGs, Then High, Then Return Low State
    GPIO.output(FRONT_GPIO, GPIO.LOW)
    time.sleep(0.1)
    GPIO.output(FRONT_GPIO, GPIO.HIGH)
    time.sleep(0.3)
    GPIO.output(FRONT_GPIO, GPIO.LOW)
    start = time.time()
    GPIO.setup(FRONT_GPIO, GPIO.IN)

    while GPIO.input(FRONT_GPIO) == 0:
        start = time.time()

    while GPIO.input(FRONT_GPIO) == 1:
        stop = time.time()

    elapsed = stop-start
    global fdist
    fdist = elapsed * 34300
    fdist = fdist/2
    print("Ultrasonic Measurement From Front Sensor - 1")
    print("fdist : %.1f CM" % fdist)

    # Left Corner

    GPIO.output(LEFT_CORNER_GPIO, GPIO.LOW)
    time.sleep(0.1)
    GPIO.output(LEFT_CORNER_GPIO, GPIO.HIGH)
    time.sleep(0.3)
    GPIO.output(LEFT_CORNER_GPIO, GPIO.LOW)
    start2 = time.time()
    GPIO.setup(LEFT_CORNER_GPIO, GPIO.IN)

    while GPIO.input(LEFT_CORNER_GPIO) == 0:
        start2 = time.time()

    while GPIO.input(LEFT_CORNER_GPIO) == 1:
        stop2 = time.time()

    elapsed2 = stop2-start2
    global ldist
    ldist = elapsed2 * 34300
    ldist = ldist/2
    print("Ultrasonic Measurement From Left Corner Sensor - 2")
    print("fdist : %.1f CM" % ldist)

    # Right Corner

    GPIO.output(RIGHT_CORNER_GPIO, GPIO.LOW)
    time.sleep(0.1)
    GPIO.output(RIGHT_CORNER_GPIO, GPIO.HIGH)
    time.sleep(0.3)
    GPIO.output(RIGHT_CORNER_GPIO, GPIO.LOW)
    start = time.time()
    GPIO.setup(RIGHT_CORNER_GPIO, GPIO.IN)

    while GPIO.input(RIGHT_CORNER_GPIO) == 0:
        start3 = time.time()

    while GPIO.input(RIGHT_CORNER_GPIO) == 1:
        stop3 = time.time()

    elapsed3 = stop3-start3
    global rdist
    rdist = elapsed3 * 34300
    rdist = rdist/2
    print("Ultrasonic Measurement From Right Corner Sensor - 3")
    print("fdist : %.1f CM" % rdist)

    return fdist, ldist, rdist

def turnL():
	ser.write("S".encode())
	time.sleep(.1)
	ser.write("L".encode())
	time.sleep(1.3)
	ser.write("S".encode())
	time.sleep(.1)
	ser.write("F".encode())
	time.sleep(1.5)
	ser.write("S".encode())
	time.sleep(.1)
	ser.write("L".encode())
	time.sleep(1.4)
	ser.write("S".encode())
	time.sleep(.1)
	return
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
